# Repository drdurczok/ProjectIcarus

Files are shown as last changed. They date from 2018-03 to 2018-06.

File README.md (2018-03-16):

# ProjectIcarus
A mechanical hand with the full dexterity of its real counterpart controlled in an intuitive way by a human. The control will be based on the idea of mimicking the operators limbs. Pairing this with a strategically placed camera and a virtual reality headset, we have an operator who is fully immersed and in full control of the situation at hand.

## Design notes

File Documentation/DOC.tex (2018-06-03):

\documentclass{article}
\usepackage{graphicx}
\usepackage{color}
\usepackage{url}
\usepackage[font=small,labelfont=bf]{caption}
\usepackage[a4paper, total={16cm, 24cm}]{geometry}
\usepackage{indentfirst}

\begin{document}

\begin{titlepage}
    \begin{center}
        
	\begin{figure}
		\centering
        FACULTY OF MECHANICAL ENGINEERING AND ROBOTICS\\
        AGH UNIVERSITY OF SCIENCE AND TECHNOLOGY\\
        \vspace{0.2cm}
    	\begin{minipage}[b]{0.4\textwidth}
    	    \centering
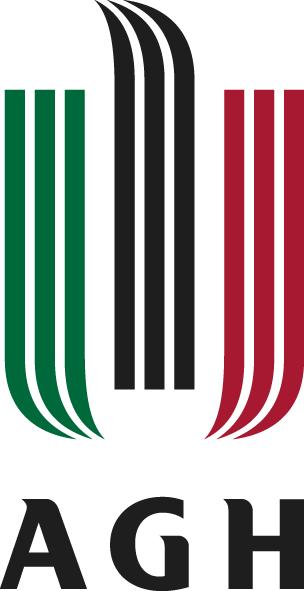
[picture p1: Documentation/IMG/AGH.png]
    		
    	\end{minipage}
    	\hfill
    	\begin{minipage}[b]{0.4\textwidth}
	    	\centering
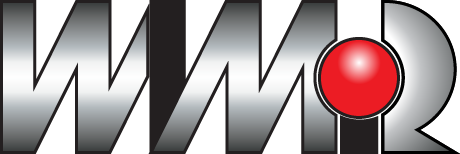
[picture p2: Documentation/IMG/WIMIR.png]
    		
		\end{minipage}
		\vspace{1cm}
    \end{figure}

    \Huge \textbf{Vision Controlled Mechanical Hand}
        
    \vspace{0.8cm}
    \LARGE 
    \color{black} 
            
    \vspace{0.8cm}       
    \textbf{Damian Durczok\\Mikolaj Gacek\\Adam Kolusz}        
    \vfill       
    \vspace{0.8cm}    
    3.06.2018
        
    \end{center}
\end{titlepage}

\tableofcontents
\break

\section{State of Art}
A typical mechatronic device encompasses many fields of technological engineering. This includes mechanical engineering, electronics, computer engineering, systems and control engineering. To thoroughly design such a system with awareness of all its elements during each step of the process requires the foresight and knowledge of all the components and relations between individual elements. This is the purpose of the state of art - a prerequisite to the initialization of a project. By the end of this section we will have explored existing technologies and solutions to our problem and drawn up a basic model of the mechatronic device.

\subsection{The Problem}
Certain situations that endanger human life benefit from the intervention of a robotic device. However, these robots may be limited in functionality compared to the human counterpart. In cases such as bomb disposal, nuclear power station decommissioning or handling of dangerous substances the dexterity of a human hand is significantly important.

\subsection{The Solution}
The mechanical hand is a device that has been iterated on many times in recent history. Control of such a hand is either by machine or human. For automated tasks, a machine controlled hand is more than sufficient. However, in unpredictable environments human intervention is still necessary.

This is where the idea stems together. A mechanical hand with the full dexterity of its real counterpart controlled in an intuitive way by a human. The control will be based on the idea of mimicking the operators limbs. Pairing this with a strategically placed camera and a virtual reality headset, we have an operator who is fully immersed and in full control of the situation at hand.

\subsection{Mechanical Hand}
Most modern innovations of the mechanical hand are related to the development of prosthetics. BeBionic \cite{bebionic} and Vincent Systems \cite{vincent} among many others have developed such devices that accurately mimic the likeness.

\begin{center}
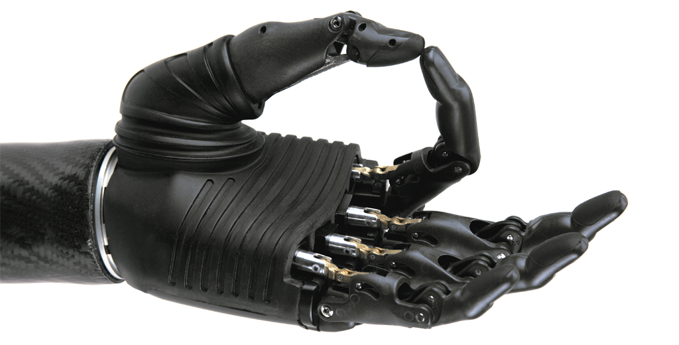
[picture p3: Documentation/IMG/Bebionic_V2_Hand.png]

\captionof{figure}{BeBionic Mechanical Hand}
\end{center}

The most popular actuation method is a combination of a DC motor and either a worm gear or lead screw. The size of the hand leaves us with a very small working area, as a result the driving motors must be very small with high gear reductions.

\begin{center}
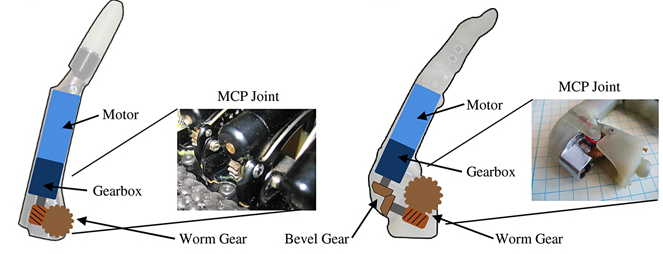
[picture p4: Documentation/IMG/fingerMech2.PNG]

\captionof{figure}{Mechanics of a finger \cite{JRRD}}
\end{center}

Another issue to contend with is the weight and speed of the mechanism. For prosthetic use, the hands are made to be lightweight for mobility. Whereas in our application this isn't a problem, we may still benefit from reducing the moments of inertia by increasing the acceleration capabilities of joints. Ideally having the same dynamic properties as the human hand.

The limited working space also forces certain optimization. For instance, not all joints need to be independently driven. We may simplify the model by involving mechanisms that create a fixed relationship between joints.

\begin{center}
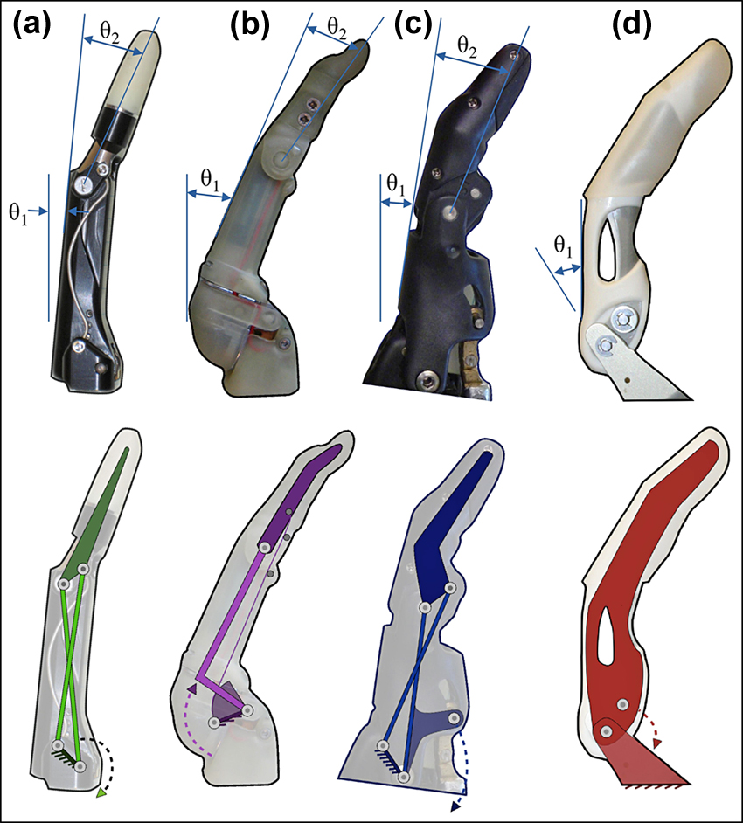
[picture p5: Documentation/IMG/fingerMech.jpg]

\captionof{figure}{Reducing degrees of freedom mechanically \cite{JRRD}}
\end{center}

A final feature commonly observed is a certain flexion compliance level. Under a certain level of pressure, the joint flexes by either a spring or flexible material. This is a protective measure to prevent the damage of certain elements.

Many hobbyists opt out for a different solution that includes a motor and line. The joints are controlled in one direction by the contraction of a line and in the other by a spring or flexible material. This greatly simplifies the design process by allowing the motors to be located elsewhere. Potentially allowing for much larger drives and a greater gripping force along with greater movement speeds and accelerations. This system also naturally includes flexion compliance.

\begin{center}

\captionof{figure}{Solidworks solution \cite{stringHand}}
\end{center}

This solution isn't as well researched as the earlier method and will require a longer prototyping phase. \\[12pt]
\indent Pneumatics may offer another solution. All the fingers are actuated by a pneumatic air muscle. These prove to have very high grip strength with favourable dynamic characteristics. All however comes with the price of size, to drive such a system a constant supply of compressed air is necessary to accurately position the stroke-length of each air muscle. Additionally a large valve system is necessary to control such a device.

\begin{center}
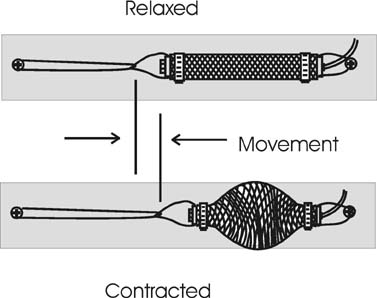
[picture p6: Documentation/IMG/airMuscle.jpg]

\captionof{figure}{Air Muscle}
\end{center}

In summary, we may consider driving our mechanism with either an electric motor or a pneumatic device. The pneumatic device may allow for much better dynamic performance such as limb velocity, acceleration and grip strength. However requires an entire pneumatic system in place which may prove expensive and resource heavy. The DC motor compromises on dynamic performance in place for a more ergonomic design.\\[12pt]
\indent The driving mechanism may be optimized by involving dependent joints. These joints may be driven directly or at a distance using lines. A line driven mechanism alleviates the problem of having to work in a small working area by removing the largest elements externally. 

\subsection{Sensors}
For the human hand to control the mechanical counterpart a set of sensors are necessary. For simplicity, we will only track the position of individual fingers. Although data sets such as grip strength, velocity or acceleration of fingers may inadvertently be natural features of some of the concepts.

A vision system introduces a non-invasive and non-contact method. Free to the public libraries such as OpenCV paired with a stereo camera system allow for creation of depth perception maps. After calibration of each camera and synchronization of frames, such a system will allow for accurate tracking.

\begin{center}
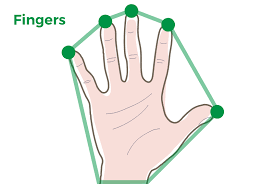
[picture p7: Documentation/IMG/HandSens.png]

\captionof{figure}{Visualization of hand recognition software}
\end{center}

\indent Microsoft released another interpretation of a motion sensing input design with the Xbox Kinect \cite{kinect}. The device includes an additional IR light source and an infrared camera for depth mapping and an RGB color VGA video camera for image recognition. The camera is capable of isolating the human from the background and with image recognition track individual limbs. The Microsoft SDK package for the system also includes access to the massive database for image recognition. This has been shown to work with small children using sign language learning software.

Plenty of other approaches also exist. One of the most popular is the usage of flex sensors. The concept is very simple, a change of resistance occurs with deflection, ie the flexing of a joint. The main disadvantage of such a solution is very low cost/efficiency ratio. However this method takes up very little space and low power consumption.

Another accurate positioning method is with the use of multiple MPUs placed in carefully selected positions. If connected via a I2C protocol we may connect many along a single bus. These sensors are quite inexpensive compared to the flex sensor and provide acceptable accuracy when paired with suitable filters such as a Kalman filter. If not taken into account, the position obtained drifts over time resulting in a high error. However this can easily be mitigated.

With a strategically placed camera and a line emitting IR blaster we may create a vision system that proves to be much more reliable than the previous concept. DIGITS \cite{Digits} is the realization of such a device. It is capable of emulating the human hand in a virtual environment with great success.

\begin{center}
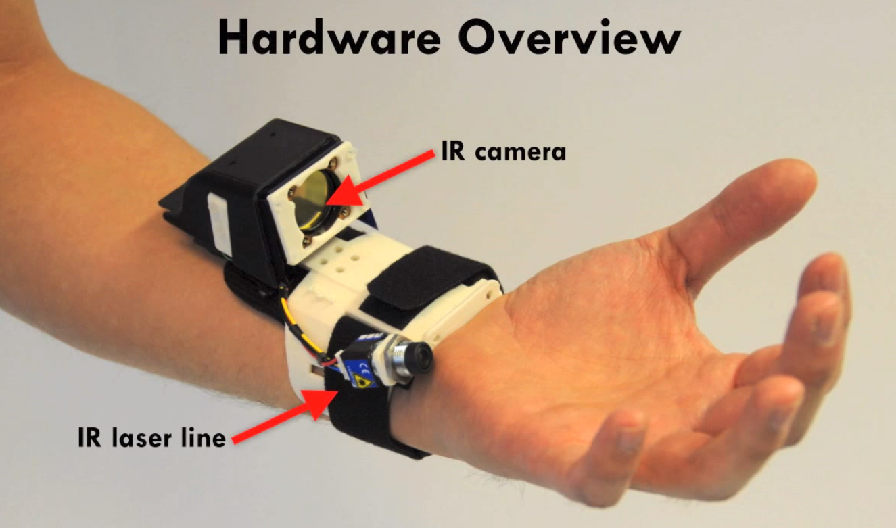
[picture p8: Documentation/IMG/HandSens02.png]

\captionof{figure}{A finger position method by Digits \cite{Digits}}
\end{center}

\indent The IR blaster greatly increases the image recognition performance by giving it obvious vision cues. The wrist mounted device may also benefit from an additional MPU sensor that will provide us with information on the placement of the arm. Such a system is not limited by the environment; lighting levels and surrounding colors wouldn't have a significant impact on the performance of the mechanism.

\subsection{Control}

For an electronic control system we may consider two distinct architectures that will be ideal for our device; an FPGA board or a microcomputer like the Raspberry Pi. Both devices are capable of image signal processing with the use of the OpenCV library, therefore all techniques discussed above are viable. In extension, OpenCL (an official and supported extension to OpenCV) can be used inplace of HDL in FPGA to improve design productivity. The main advantage of FPGA over a CPU is parallelism\cite{FPGA}. In a system where many sensors and actuators are present, and a quick response of a mechanical hand is essential this can become a major advantage over traditional microcomputers. However, this comes with a cost of complexity.

Both systems are also capable of signal filtering and noise reduction. This can reduce micro motions and sensor imperfections to create a much more fluid movement of the hand. Additionally, machine learning could incorporate a decision making process that could create precise maneuvers even if the operator isn't fully trained or capable of them.  Potentially becoming an enhanced extension of the human by providing stability and limiting the motion to avoid accidental jerks or unwanted reflexes.

\section{Concept}
\subsection{Mechanics}

The primary attributes of our mechanical hand will be its gripping capabilities and precision. To achieve this while keeping the entire project within acceptable dimensions we need to introduce dependent joints with certain flexion compliance.

Some of the dependent joints will have an additional mechanism extended from it. This mechanism will usually consist of a spring that is pushing on a lever. With no external forces, the lever will be sitting in a locked maximum position. The moment it comes into contact with something and depending on the amount of force applied, the lever hinges back. This gives the dependent joint a certain amount of restricted movement that mimics the joints of the hand in a similar fashion. This sort of compliance will greatly increase the hands holding capabilities by being able to mechanically adapt to the objects geometrical features.

A single hand will be comprised of three digits, each with two degrees of controlled motion. However, due to flexion compliance it will have many more degrees of freedom. The human hand has four bones for each finger and three for the thumb. The bones go as follows from the tip of the finger to the wrist; distal phalanges, medial phalanges, proximal phalanges and the metacarpals. With the thumb lacking the medial phalanges. Each finger has four degrees of freedom except for the thumb by only having three. Next we will explore all our joints and describe how we plan to resolve them. 

The first is the opposable thumb, which will have two joints and one degree of controlled motion. The distal phalanges will have flexion compliance, while the metacarpal will be driven by a larger motor to match the cumulative force of the other joints. The thumb needs to be as universal as its counterpart. Both grip strength and precision tasks paired with the other fingers are important. 

The index finger will have four joints and also two degrees of motion. The distal phalanges will have 90 degree flexion compliance and is dependent on the angle of the medial phalanges. The medial phalanges and proximal phalanges will be each driven by a motor, while the metacarpals will be attached by ball joint and given minimal flexion compliance.

The final three fingers will be combined into one larger finger. Since these fingers are usually used for gripping and handling of objects, they will be mounted with larger motors and the larger surface area will provide a better gripping surface. The joint mobility will be similar to the index finger.

The last area to cover is the palm. The metacarpals is responsibly for its shape. We have two metacarpals that have flexion compliance and one on the thumb that is driven. This means the palm has the capability of adjusting its shape to a gripped object.

\subsection{Control and Sensors}

With the mechanical end of the project providing advantages gripping mechanisms and variable grip strength, the control of the device may be much more forgiving and the use of haptic feedback isn't as necessary. With this in mind, we may create a completely non invasive human operated controller with the use of vision systems.

The system will be made up of two cameras that will provide stereo vision. With proper calibration, we may produce a depth map and isolate a human operator from the background. Once isolated, it is a matter of manipulating the image and developing algorithms that may track geometrical features. Libraries such as OpenCV already provide most of these features in languages such as Python and C++.

The readings from the camera may be further improved by adding a layer of machine decision making. Certain filters for noise reduction are certainly necessary, however we may also include pre-programmed operations that may assist the human and become an extension of him. For instance, we may limit the velocity of fingers to reduce abrupt movements in certain situations or remember the gripping position for a certain object. This way the operator carries out the general movement required of the robot and the robot decides on the precise movements that may be difficult for the user to control. 

\subsection{Electronics and Actuating}

Since the image signals from two cameras have to be processed in real-time it is important to consider a capable computer. We decided that the entire Vision System will be run on Raspberry Pi 3 Model B microcomputer. This device possesses a quad-core 64bit processor and 1GB RAM, hence is capable of performing desired operations. Further reassurance of its capabilities is the many camera modules and OpenCV projects already developed for the Raspberry.

The robotic fingers will be actuated by six servomotors controlled by an Arduino Uno R3 attached to the hand. The Arduino Uno R3 has 14 digital input/output pins (of which 6 can be used as PWM outputs). The wireless connection between the Raspberry Pi 3 B and the Arduino will be implemented with the use of a Bluetooth protocol. The Raspberry has a built-in Bluetooth module and Arduino can be easily extended with a HC-0x series Bluetooth module.

The Arduino controller and motors will be energized by an individual power supply with a voltage stabilizer. The Raspberry Pi will be energized by a set of 18650 cells through a voltage stabilizer.

\break
\section{Software}
\subsection{Requirements}
Requirements analysis is the first stage in the systems engineering process and software development process. The software requirements specification (SRS) lays out functional and non-functional requirements, and may include a set of use-cases that describe user interactions that the software must provide. We will carry out such an analysis on our system.

The purpose of this software is simple, to track the movements of a human hand. Specifically, we need to obtain certain points correlated to the human hand that satisfy our kinematic equations. The system will have to operate in real time with minimal delays. This system must also be non-invasive and work reliable in many different environments. Our solution implements a vision system. The general structure will look as such; capture footage, process the video feed, analyze the data and implement filters or statistical methods to improve the tracking. The product must work with minimum product knowledge, so called plug-and-play.

The user will interact with the system through both the vision system and voice controls. The camera system will be operating at a distance from the user, therefore to implement a user interface that is convenient to use and continues to be non-invasive and non-contact, as the hands are preoccupied, we will be relying on voice actuation. This will provide basic functionality on top of the core tracking service. 

We will also be communicating with another device, which in turn is responsible for controlling the mechanical hand. The information processed by our software will provide the secondary device with the information it needs to carry out the inverse kinematic calculations. This information will be in the form of coordinate points. This process must be robust with very fast response time. The quality of the point detection must be reliable and stable. It must also be tolerant to any user mistakes.

Additional limitations to our software will involve the hardware it will be run on. Our system will be limited to the capabilities of the Raspberry Pi, as well as the available libraries. Our vision system will be built on the OpenCv library, while our voice actuation on the Sphinx libraries. Both libraries support C++ and Java.\vspace{12pt}

The software aims to provide natural control for complex end-effectors. The human brain is very good at calculating inverse kinematics of its own body, to the point where it is completely natural to us without much thought. By taking advantage of this, we may quicken the learning process for controlling advanced machinery and allow for much more complex maneuverability. Controlling a mechanical hand is one possible use-case, however by selecting what points and how many points are to be tracked, this software may be used for many different types of control, not necessarily mechanical. The software may be just as easily used for gesture control or interpreting sign language. Extensibility needs to be considered during the design process. Additionally, we may provide options for several different supported cameras and tracking modules and expand these features over time with software updates.

\subsection{Implementation}
We may break our entire software apart into several subcategories; vision system, vision system calibration, audio system and audio system calibration. The calibration software will be used by the developers to prepare certain models to work with our software, this will be discussed in much more detail below. The user will be interacting exclusively with our vision and audio software.
\subsubsection{Vision System Calibration}
The calibration process is made up of several key steps depending on the technology used. First let us look at the calibration of a stereo camera setup for the creation of disparity maps. We begin by calculating the intrinsic parameters of each camera, this includes the focal length, principle points and consequently the distortion coefficients. We use this information to undistort each individual camera. Following this, we need to calculate the extrinsic parameters. During this process we acquire information of where one camera is with respect to the other, this includes the rotation and translation matrix. From this we additionally acquire the fundamental and essential matrix, which in turn gives us the rectification parameters. After rectifying the images, we will have matching epipolar lines in each camera and we may begin the disparity mapping process. The disparity map gives us clear information on the hands location and its shape. The actual tracking software will be discussed later.

\begin{figure}[!hb]
    \begin{minipage}[b]{0.49\textwidth}
    	   \centering
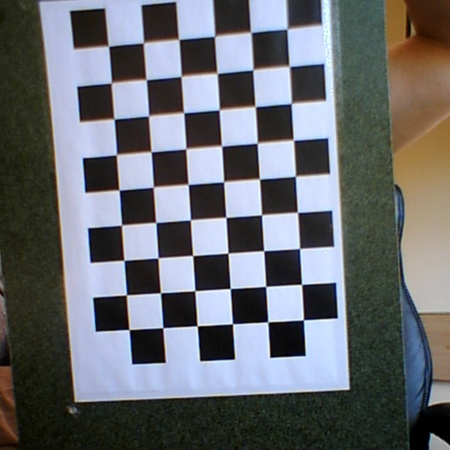
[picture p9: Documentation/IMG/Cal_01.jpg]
		
		\captionof{figure}{Calibration Image}
	\end{minipage}
    \hfill
    \begin{minipage}[b]{0.49\textwidth}
	    \centering
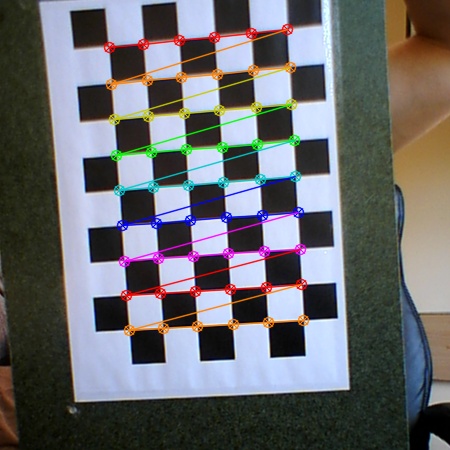
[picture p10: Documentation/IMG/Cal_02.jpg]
		
		\captionof{figure}{Calibration Image With Overlay}    	
	\end{minipage}
\end{figure}

In the case of an IR blaster setup, the calibration will look slightly different. Since we will only be using one camera to create a disparity map, the calibration will be much simpler. After calculating the intrinsic parameters, the camera should be ready.
\subsubsection{Vision System}
The vision system will be comprised of several steps. The first being to discern the hand from other objects and background noise. This will be done with the use of disparity maps and thresholds. After obtaining a clearly defined silhouette of the object to be tracked, we focus on the original video feed again and pattern the singled out area with a grid of points. These points will be used in our Lucas-Kanade tracking algorithm that will create optical flow vectors for each of the given points. This will provide us with displacement and velocity information. The next step requires another set of algorithms that first filter any errors in the optical flow map and then using statistical methods returns a few individual points that correspond to the hands position in 3D space.

\begin{center}
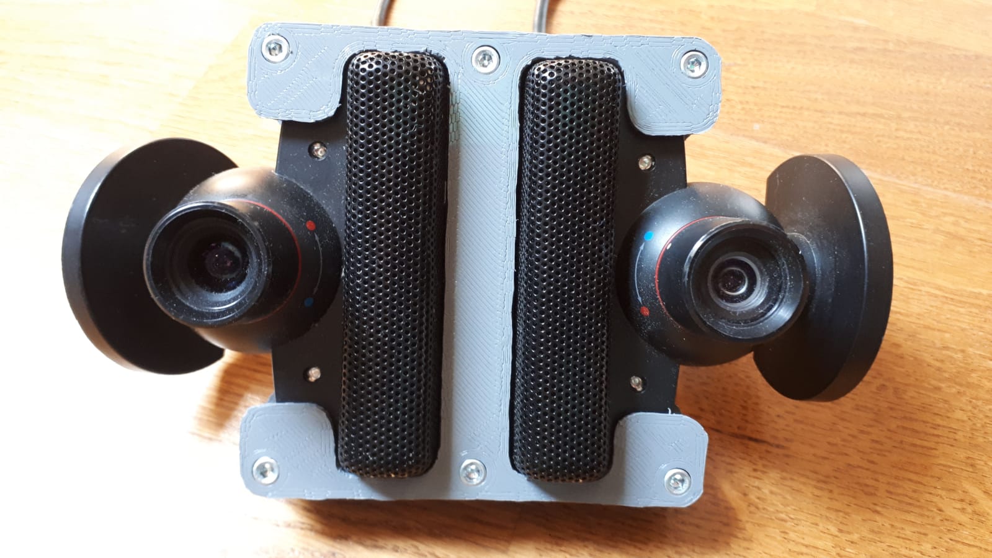
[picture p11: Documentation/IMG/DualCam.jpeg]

\captionof{figure}{Dual Camera Setup}	
\end{center}

\break
Here we may compare the two very different technologies. The dual camera system relies on very precise calibration to create accurate epipolar lines. These lines reduce the number of calculations needed to find matching points as they are used as lines along which the pixels are compared between images. That is why we have noise present along what seems like horizontal lines, better calibration would reduce those. A disadvantage of such a system is that there needs to be consistent light levels for this to work. Most environments do not provide a bright and reliable light source, therefore some additional preparation is necessary for such a system to work consistently.

The Kinect on the other hand uses infrared light to create a grid of points. It uses its IR camera to measure the size of various points and gauge their distance. Based on all this data it is capable of creating a disparity map. Additionally, since it creates its own source of invisible light, it will work in various situations where the dual camera set-up wouldn't. The Kinect relies on complex algorithms only provided by Microsoft Windows and their SDK packages. The reason the Kinect is so reliable is because of the machine learning done at Micosoft to make the software capable of such tasks.

\begin{center}
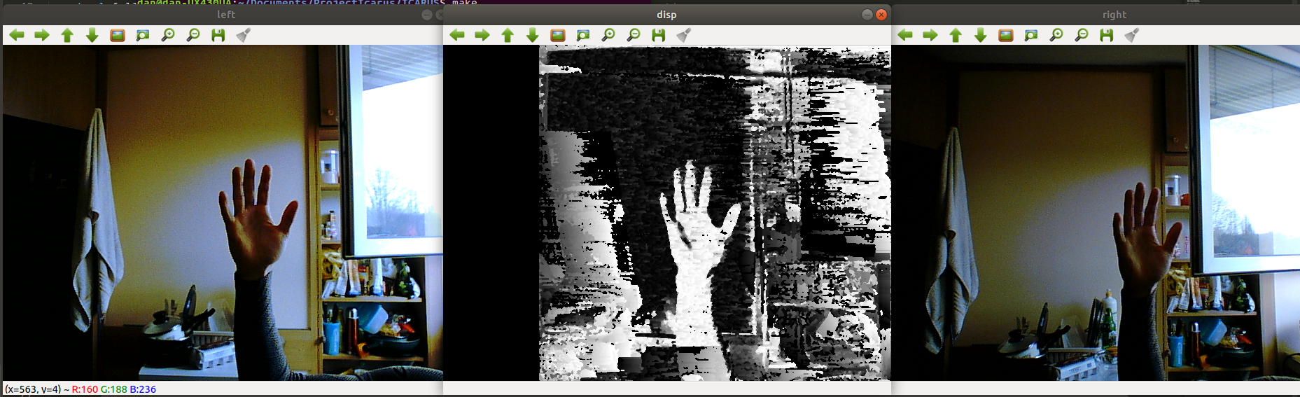
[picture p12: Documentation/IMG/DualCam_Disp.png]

\captionof{figure}{Dual Camera Disparity Map}   	
\end{center}

\begin{figure}[!hb]
    \begin{minipage}[b]{0.49\textwidth}
    	   \centering
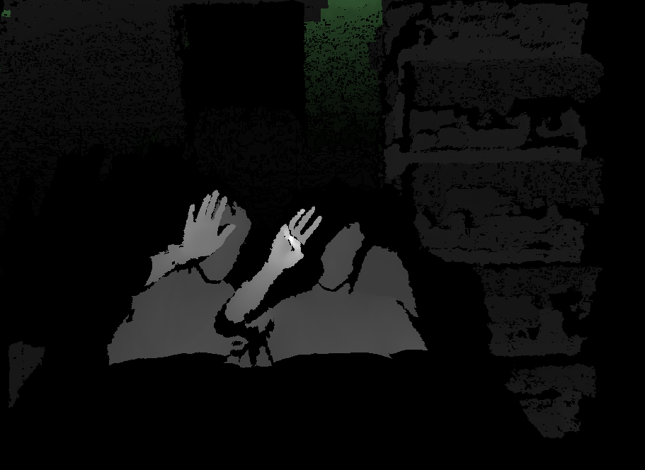
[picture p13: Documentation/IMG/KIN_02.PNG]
		
	\end{minipage}
    \hfill
    \begin{minipage}[b]{0.49\textwidth}
	    \centering
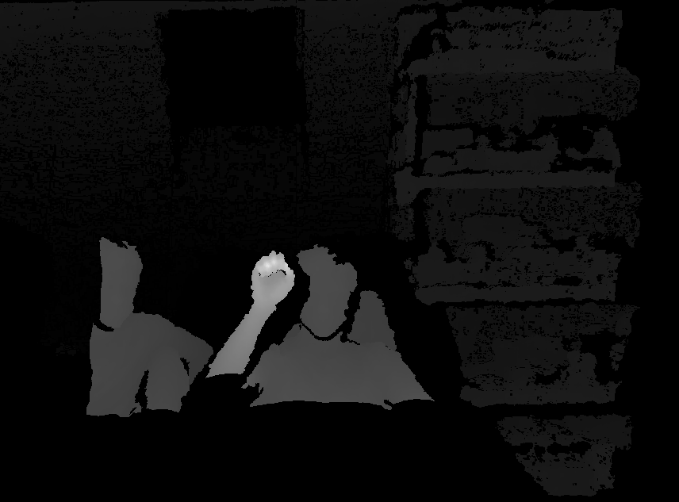
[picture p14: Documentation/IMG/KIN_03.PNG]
		
	\end{minipage}
	\captionof{figure}{Kinect Disparity Map}
\end{figure}

\subsubsection{Audio System}
The general process of the application consists of several key steps. We begin with interval audio recordings. After each interval recording, it decodes the .raw file and searches for a keyword. If the keyword was spoken, the recording re-initiates. The second .raw file is decoded to receive a string. This string needs to be compared to the applications look up table. The final part is the calling of the function which is most appropriate based on the returned string. 
Many other classes make up the individual actions of the application. These “action” classes are very easy to add and are what makes the program modular. 
To accomplish all of this we needed to take advantage of language and audio processing API’s. These are briefly introduced and summarized below:

\paragraph{PocketSphinx} 
Pocket-Sphinx is a lightweight speech recognition engine, specifically tuned for handheld and mobile devices. The libraries are written in C and are dependent on the Sphinx-Base library. \vspace{12pt}

\noindent For the library to function properly, we need to provide additional models and dictionaries:
\begin{itemize}
	\item Acoustic model: The acoustic model models the sound of a phone, it translates recorded sounds into labeled phones. Usually a hmm is used. Each phone has a hmm. 
	\item Phonetic dictionary: Maps phones to words.
	\item Language model: Used to determine sequences of words that are allowed. 
\end{itemize}

\noindent Most models require training to be more accurate:
\begin{enumerate}
	\item Acoustic models require lots of recordings of people saying words and sentences (not that difficult to do) and accurate transcription of the recordings (time consuming). It is possible to take an existing model and quickly adapt it to a particular speaker.
	\item Language models require for different systems different language models. Different applications need to recognize different sets of words.
	\item The performance of the recognizer is significantly improved if your language model only considers relevant words to your application.
	\item You can take an existing language model and trim it to what you need, or make on from scratch using the JSGF format.
\end{enumerate}

Words are a sequences of sounds, where each sound is a phone. However, the exact pronunciation of a phone depends on the phones before and after.
Diphones are two phones. Diphones are less impacted by the phones that come before or after. 
Senones are triphones and quinphones.
While there are many phones, not all combinations of a phone is a word. Thus, we should not simply recognize phones, but we need to recognize words which are sequences of phones.
Besides phones are fillers (ex., breath, “um”). An utterance is a sequence of words and fillers. Utterances are separated by a pause.

\paragraph{ALSA(Advanced Linux Sound Architecture)}
Sound is converted to its electrical form by a transducer, such as a microphone. An analog-to-digital converter (ADC) converts the analog voltages into discrete values, called samples, at regular intervals in time, known as the sampling rate. By sending the samples to a digital-to-analog converter and an output transducer, such as a loudspeaker, the original sound can be reproduced.

The size of the samples, expressed in bits, is one factor that determines how accurately the sound is represented in digital form. The other major factor affecting sound quality is the sampling rate. The Nyquist Theorem states that the highest frequency that can be represented accurately is at most one-half the sampling rate. 

We will mostly be interested in the PCM interface: the interface for managing digital audio capture and playback. 

 A sound card has a hardware buffer that stores recorded samples. When the buffer is sufficiently full, it generates an interrupt. The kernel sound driver then uses direct memory access (DMA) to transfer samples to an application buffer in memory. Similarly, for playback, another application buffer is transferred from memory to the sound card's hardware buffer using DMA.
 
These hardware buffers are ring buffers, meaning the data wraps back to the start when the end of the buffer is reached. A pointer is maintained to keep track of the current positions in both the hardware buffer and the application buffer. Outside of the kernel, only the application buffer is of interest, so from here on we discuss only the application buffer.
The size of the buffer can be programmed by ALSA library calls. The buffer can be quite large, and transferring it in one operation could result in unacceptable delays, called latency. To solve this, ALSA splits the buffer up into a series of periods and transfers the data in units of a period.
A period stores frames, each of which contains the samples captured at one point in time. For a stereo device, the frame would contain samples for two channels.

\begin{figure}[!hb]
    \begin{minipage}[b]{0.49\textwidth}
    	\centering
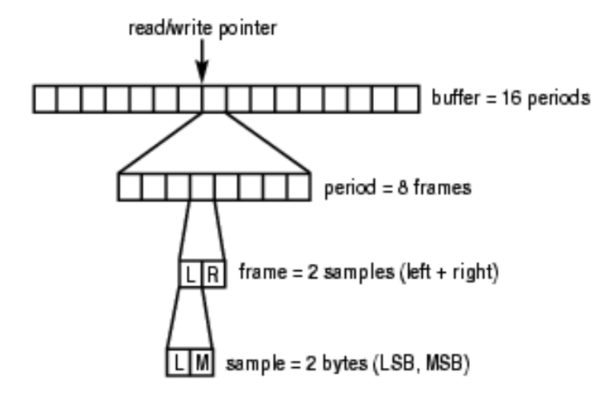
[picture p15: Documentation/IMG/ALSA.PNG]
		   	
	\end{minipage}
    \hfill
    \begin{minipage}[b]{0.49\textwidth}
		The Application Buffer (Over and Under Run), illustrates the breakdown of a buffer into periods, frames and samples with some hypothetical values. Here, left and right channel information is stored alternately within a frame; this is called interleaved mode. A non-interleaved mode, where all the sample data for one channel is stored followed by the data for the next channel, also is supported.\vspace{12pt} 	
	\end{minipage}
\end{figure}

When a sound device is active, data is transferred continuously between the hardware and application buffers. In the case of data capture (recording), if the application does not read the data in the buffer rapidly enough, the circular buffer is overwritten with new data. The resulting data loss is known as overrun. During playback, if the application does not pass data into the buffer quickly enough, it becomes starved for data, resulting in an error called underrun. The ALSA documentation sometimes refers to both of these conditions using the term XRUN. Properly designed applications can minimize XRUN and recover if it occurs.

\noindent Programs that use the PCM interface generally follow this pseudo-code:
\begin{itemize}
	\item open interface for capture or playback
	\item set hardware parameters (access mode, data format, channels, rate, etc.)
	\item while there is data to be processed:
	\begin{itemize}
		\item read PCM data (capture)
		\item write PCM data (playback)
	\end{itemize}
	\item close interface
\end{itemize}
	
When we open the PCM stream, we specify the mode as SND\textunderscore PC\textunderscore STREAM\textunderscore CAPTURE. In the main processing loop, we read the samples from the sound hardware using snd\textunderscore pcm\textunderscore readi and write it to standard output using write. 

In order to set the hardware parameters for the stream, we need to allocate a variable of type snd\textunderscore pcm\textunderscore hw\textunderscore params\textunderscore t. We do this with the macro snd\textunderscore pcm\textunderscore hw\textunderscore params\textunderscore alloca. Next, we initialize the variable using the function snd\textunderscore pcm\textunderscore hw\textunderscore params\textunderscore any, passing the previously opened PCM stream. 

We now set the desired hardware parameters using API calls that take the PCM stream handle, the hardware parameters structure and the parameter value. We set the stream to interleaved mode, 16-bit sample size, 1 channel and a 44,100 bps sampling rate. In the case of the sampling rate, sound hardware is not always able to support every sampling rate exactly. We use the function snd\textunderscore pcm\textunderscore hw\textunderscore params\textunderscore set\textunderscore rate\textunderscore near to request the nearest supported sampling rate to the requested value. The hardware parameters are not actually made active until we call the function snd\textunderscore pcm\textunderscore hw\textunderscore params.

\break
\section{Kinematics}
\subsection{Index Finger}
We will begin the analysis with the index finger. The mechanical finger may be represented by a simplified kinematic model presented below. Our system has two degrees of freedom, however the structure is much more complicated due to various lever systems and dependent angles. To simplify our mechanism, we may divide the system into four subsystems. Each system will have its own set of equations that will eventually be put together in a programming environment to define the movement of the finger.

\begin{center}
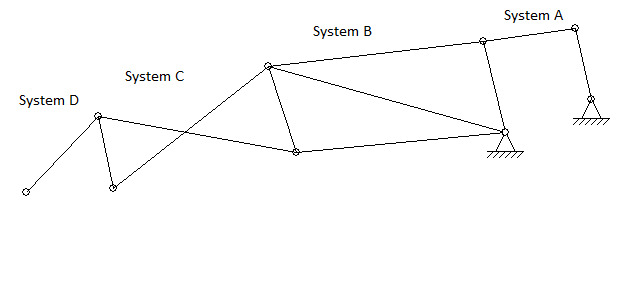
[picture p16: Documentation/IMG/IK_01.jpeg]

\captionof{figure}{Kinematic Model}	   	
\end{center}

Inverse kinematics for system A. This system is a simple 4 bar linkage mechanism that consists of a crank, coupler, rocker and frame. The motor attaches to the crank and drives the proximal phalange. The motor angle $\varphi$ drives $\alpha$, therefore the inverse kinematic formula has only one unknown variable $\alpha$ that is provided by system B. The rest of the formula consists of constants that are properties of the system. \textbf{\textit{All calculations are provided in the appendix.}}

\begin{center}
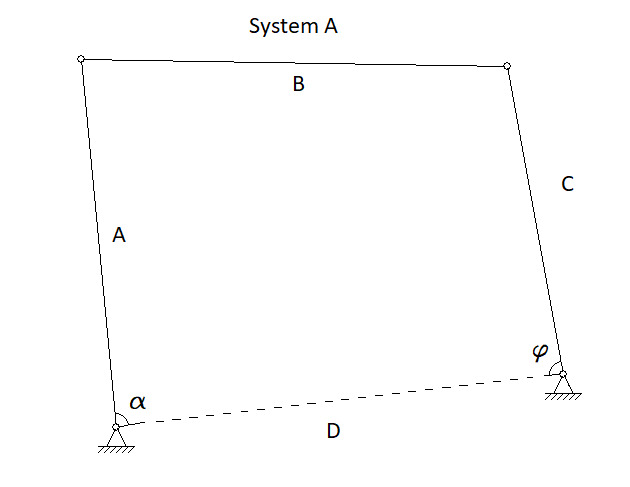
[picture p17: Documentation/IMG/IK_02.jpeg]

\captionof{figure}{4 bar linkage mechanism}	   	
\end{center}

\[ \varphi = sin^{-1} \bigg(\frac{Asin\alpha}{\sqrt{A^2+D^2-2ADcos\alpha}}\bigg) + cos^{-1} \bigg(\frac{A^2+D^2-2ADcos\alpha-B^2+C^2}{2C\sqrt{A^2+D^2-2ADcos\alpha}}\bigg)\]

Inverse kinematics for system B. This is the simplest possible system being a simple lever. However due to the software constraints, we have to additionally consider the orientation of the base coordinate system (the palm) and the offset from the motors 0 degree position. The formula is provided with the X coordinate from the camera system and based on this information figures out the angle on the four bar linkage mechanism.

\begin{center}
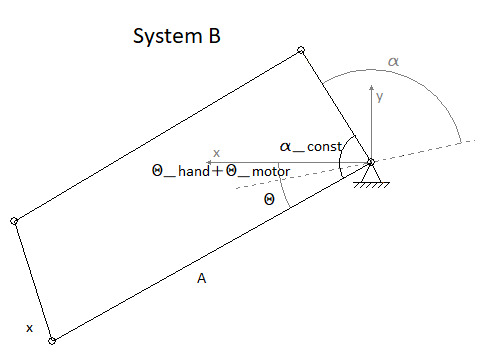
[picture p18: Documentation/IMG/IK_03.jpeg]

\captionof{figure}{Proximal Phalange}	   	
\end{center}

\[ \alpha = cos^{-1}\bigg(\frac{X}{A}\bigg) - (\theta_{hand} + \theta_{motor}) + (\pi - \alpha_{const}) \]

Provided the two equation above, we have everything we need to control the proximal phalange with the first servo motor. The servo motor is controlled entirely by one X axis coordinate provided by the software. The equations take into account various offsets, such as the orientation of the palm, as well as properties of the system such as orientation of the motor. To optimize the geometry, we may use the first equation to equate a certain rotation of the motor to the angular displacement of the finger.\vspace{12pt}

The second part of the finger is much more complicated. The mechanism is a crossed four bar linkage, which significantly complicates the equations. First we will provide several formulas that create dependencies between various angles of the mechanism.

\begin{center}
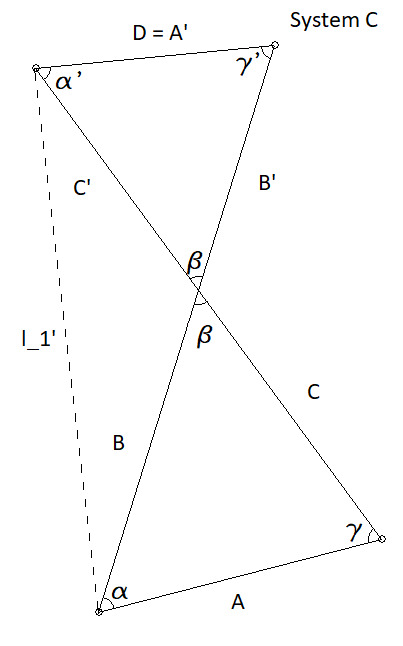
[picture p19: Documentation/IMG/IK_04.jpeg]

\captionof{figure}{Crossed 4 bar linkage mechanism}	   	
\end{center}

This formula provides us with the length the driving string needs to shorten. The only unknown is $\gamma$.
\[ l_1' = \sqrt{A^2+C^2-2ACcos\gamma}\]

This formula is taken as a proportion of the two triangles formed by the crossed mechanism. It helps us relate opposite angles.
\[ C' = \frac{CA'}{A} \frac{sin\gamma'}{sin\gamma} \]

Based on the equations above and a few more tricks, we are able to relate both angles from one side of the crossed four bar linkage mechanism. At this point we have all the information required to continue our calculations.
\[ \gamma' = cos^{-1}\bigg( \frac{-A^2+B^2-C^2+D^2+2ACcos\gamma}{-2CD} \bigg)\]

\[ \alpha = sin^{-1} \bigg( \sqrt{\frac{Bsin\gamma-(C-C')sin\gamma'}{C'}} \bigg) \]

The formula above may be used for an inverse kinematic system for the medial phalange, which is what is included in the Arduino. The last formula is much too complicated to derive for an inverse kinematic system, therefore a numeric solution is necessary. With the forward kinematic equation below, we may create a look up table and relate both $\gamma'$ and $\alpha$ to $\gamma$ which in turn provides us with the necessary information to calculate the shortening of the string and movement of the motor.

\begin{center}
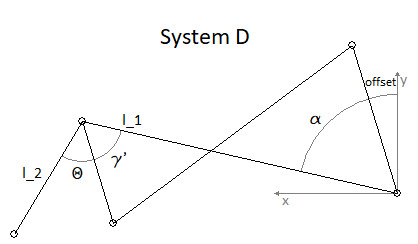
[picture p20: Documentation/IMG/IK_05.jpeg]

\captionof{figure}{Distal Phalange}	   	
\end{center}

\[ X = l_1 cos(\alpha+offsets) - l_2 cos(\gamma') \]

\subsection{Thumb}
Although the thumb has two degrees of freedom as in the previous example, it is much simpler. Both joints are rotational, however in two different planes. The forward kinematics as well as the inverse kinematics are both relatively simple.

\begin{figure}[!hb]
    \begin{minipage}[b]{0.49\textwidth}
    	\centering
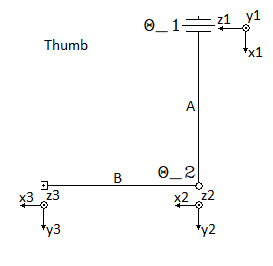
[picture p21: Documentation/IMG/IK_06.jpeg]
		
	\end{minipage}
    \hfill
    \begin{minipage}[b]{0.49\textwidth}
		\[ \theta_1 = cos^{-1}\bigg(\frac{X_3}{A}+B*sin(\theta_2)\bigg)\]
		\[ \theta_2 = cos^{-1}\bigg(\frac{X_2}{B}\bigg) \]\vspace{80pt} 	
	\end{minipage}
\end{figure}

\subsection{Arduino}
The formulas derived earlier are for the purpose of controlling the hand, therefore they need a controller. The Arduino Nano is the board of choice being that it is very similar to the Arduino UNO (where all the testing was done) and is very compact. The Atmega328's 8-bit CPU running at 16MHz is more than sufficient for calculating our equations in real time. The Nano has only 6 PWM pins, however the provided servo libraries support many more. A servo only requires a pulse 1ms long, so a driving frequency of 1kHz is needed. Such a frequency is easily accomplished by the integrated CPU and we may actually use any of the outputs on the device. The 14 digital pins and 8 analog summed up for a total of 22 pins is more than sufficient for wiring up our device. The servo motors are powered by an external power supply, therefore the Arduino Nano has the sole task of controlling the motors.

\begin{center}
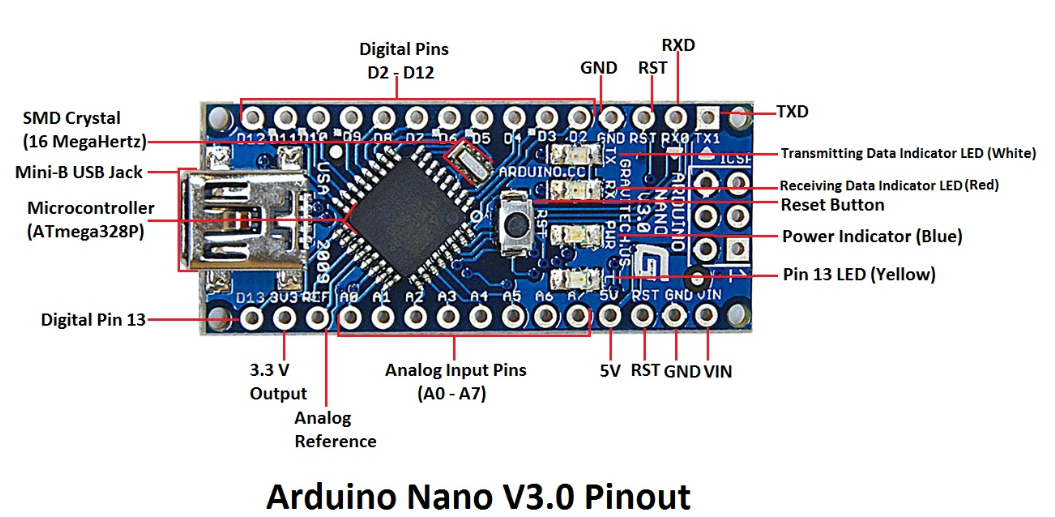
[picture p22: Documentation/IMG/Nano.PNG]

\end{center}

An external device will provide the parameters necessary for our equations. We will  now review the code structure. For each motor, there exists a separate INO file that contains all the necessary equations and conversions in reusable methods. This allows us to reuse many of the formulas for fingers with the same kinematics. Additionally, there exist parameter files that carry the mechanisms properties. Our external input device provides us with the X coordinates for each motor. There is one input, a coordinate, and one output, the angle of the motor, per servo.

There exist only two different mechanism, the thumb and index finger. Therefore four different kinematic structures for two degree of freedom mechanisms. The index finger is reusable, varying only in mechanical properties in configuration files. Each INO file has a debugging tool that displays various values of interest. Below we may find the first one for the proximal phalange of the index finger.

\begin{center}
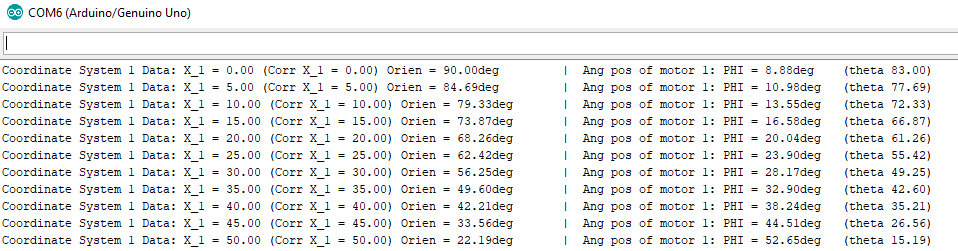
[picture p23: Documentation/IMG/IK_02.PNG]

\end{center}

We may interpret the data in the following fashion. The X1 information is provided by the external device as input to our code. If X1 is zero, this means it is at a 90 degree angle to the world coordinate system (or if palm orientation compensation is disabled, 90 degrees to the palm). The corrected X1 value takes into account angular offsets, for instance if the palm is angled, so is the world coordinate system and the X1 value needs to be properly adjusted to accurately represent the data. The angle of the motor is PHI, the data was compared to the real world range of motion and proves to be correct. If we look at X1 = 0, we may notice the motor starts at 8 degrees. This is because the motor is offset from the base coordinate system and this needs to be taken into account as we did in the kinematic formulas. The mechanical properties INO file contains additional sketches that demonstrate the exact locations of parameters.

We may now take a look at the medial and proximal phalange drive of the index finger.

\begin{center}
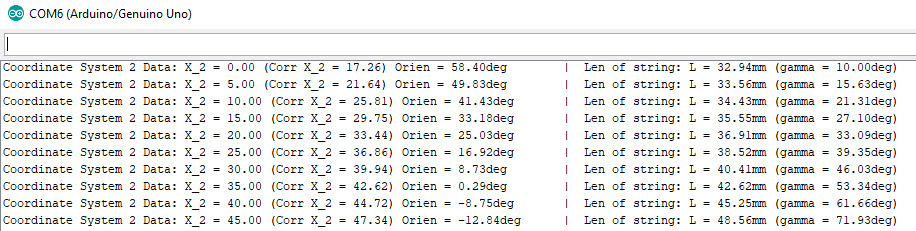
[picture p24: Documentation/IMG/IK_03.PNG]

\end{center}

The layout of the data follows suite. Instead of the angle of the motor, we derive the amount the driving string is shortened. Once again the data correlates to real world measurements. By calculating the length of the string, we are free to write any method to accompany our driving motor mechanism. In the case of the servo, we will simply wind a string around a disk. This data also considers the orientation of the previous system involving the proximal phalange. The input value is corrected and used for processing. 

The thumb is the simplest mechanism, we only have two equations, two inputs and two outputs. The formula provided above was coded into a method and reliably controls our motors.

\subsubsection{Communications}
The Arduino Nano communicates with the PC through the mini-B USB connection serial port. The connection is established in the setup() function by a method Serial.begin (). This method possess one argument, speed of serial connection (default is 9600 bits per second). The method Serial.print() prints data to the serial port as human-readable ASCII text.

Besides a direct PC connection through USB which is usually used for debugging, we may also connect wirelessly through a Bluetooth connection. For this we need an additional module for the Arduino. Arduino allows us to have multiple serial connections with different speeds, so the communication with a bluetooth device HC-6 is done through universal asynchronous receiver-transmitter (UART) on 2 pins: rx and tx (receiver and transmitter). This may be seen below.

\begin{figure}[!hb]
    \begin{minipage}[b]{0.49\textwidth}
    	\centering
		
		\captionof{figure}{Bluetooth Module Wiring}	   	
	\end{minipage}
    \hfill
    \begin{minipage}[b]{0.49\textwidth}
    	\centering
		
		\captionof{figure}{Bluetooth Module Code}   	
	\end{minipage}
\end{figure}

\break
\section{Hand Prototype}
With the kinematics and control method vigorously defined, we may put together a prototype for the mechanical hand and create simulations to test whether it will meet our requirements.

The mechanical hand needs to have the full dexterity of the human hand, which means that the mechanism dimensions need to be chosen so the range of motion is proper. Additionally, we must maintain the same speeds and accelerations as its flesh counterpart. For this it is important to select a lightweight material and motors. We may make use of an FDM printer to develop a versatile model out of PLA plastic. This solution is the fastest, cheapest and allows for rapid prototyping. The joints are made of smooth metal rods, which may help in fluid motion by reducing joint friction.

In order to assure our model is lightweight and has similar characteristics to the human hand, we needed to use compact, light but powerful motors. As motors can be rather expensive, we also needed to factor in price. We decided to go for SG92R as it fulfills enough requirements for the prototype and it is the best in its price range. Having 2.5kg*cm torque and 180deg movement range it is sufficient for demonstration of mechanics. Simulations in Solidworks confirm the geometry allows for velocities about half that of the real human hand. Below are two plots, one graphed by our hand, the other measurements taken from a human hand. We may see the velocity curve is similar, therefore our mechanics will allow for realistic movement. The peek speed was 414 mm/sec at about 45 degree angle in our situation.

\begin{figure}[!hb]
    \begin{minipage}[b]{0.49\textwidth}
    	\centering
		
		\captionof{figure}{Velocity Plot of Simulated Kinematics}	   	
	\end{minipage}
    \hfill
    \begin{minipage}[b]{0.49\textwidth}
    	\centering
		
		\captionof{figure}{Velocity Plot of Human Hand}   	
	\end{minipage}
\end{figure}

The inbuilt simulation software allows us to animate the assembly and check its range of motion. We also were able to obtain accelerations and displacements of each joint required to check if the kinematic model was correct. 

\begin{figure}[!hb]
    \begin{minipage}[b]{0.49\textwidth}
    	\centering
		
		\captionof{figure}{Acceleration Plot of Simulated Kinematics}	   	
	\end{minipage}
    \hfill
    \begin{minipage}[b]{0.49\textwidth}
    	\centering
		
		\captionof{figure}{Displacement Plot of Human Hand}   	
	\end{minipage}
\end{figure}

\break
With the requirements defined and various solutions provided, we may develop a model in CAD software. During the design process, we must keep in mind that the parts must be printable on a FDM printer. Our software of choice is Solidworks as it carries additional features such as simulations and renderings that may greatly assist us in the prototyping phase. Below we may view some images of the first prototype.

\begin{figure}[!hb]
    \begin{minipage}[b]{0.49\textwidth}
    	\centering
		
	\end{minipage}
    \hfill
    \begin{minipage}[b]{0.49\textwidth}
    	\centering
		
	\end{minipage}
\end{figure}

FEM analysis performed allowed us to find the maximum force a single finger can output. It is about 8.23N so when the filament Fiberflex 40D that will be covering the fingertips to increase the grip strength  we can grab objects in range of 100-400grams, depending on the material that it is from. See table below for multiplicands that set the output force. 

\begin{center}


\end{center}

Additional design considerations include a self locking mechanism, so when the hand is turned off, it keeps the open palm position. This is ensured by springs attached to the back of each finger and by servo holding torque.

\break
\section{Bills of Materials}
The below bills of materials includes all the materials used to build our working prototype. The prices provided are accessible market prices, and many of the elements where already owned or found at a lower price. The Kinect was kindly donated by Andrew Popiel from Lazy Solutions.

\begin{center}

\end{center}

\section{Future Development}
Based on the entire design process above, we may start putting together the concept for the final product. With properly working mechanics, we may continue by increasing the number of fingers. With the prototyping phase almost complete, we may also begin constructing a version with other materials. A concept was created in blender software to display the possibilities of such a hand.

\begin{figure}[!hb]
    \begin{minipage}[b]{0.49\textwidth}
    	\centering
		
	\end{minipage}
    \hfill
    \begin{minipage}[b]{0.49\textwidth}
    	\centering
		
	\end{minipage}
\end{figure}

\break
\addcontentsline{toc}{section}{References}
\begin{thebibliography}{1}
	\bibitem{bebionic} BeBionic. Retrieved from {\url{http://bebionic.com/the_hand/technical_information/}} 
	\bibitem{vincent} VincentSystems. Retrieved from {\url{  https://vincentsystems.de/en/}} 
	\bibitem{JRRD} U.S. Department of Veterans Affairs, {\em Journal of Rehabilitation Research And Development}. Volume 50 Number 5, 2013
   Pages 599-618 Retrieved form {\url{https://www.rehab.research.va.gov/jour/2013/505/page599.html}}
	\bibitem{stringHand} SOLIDWORKS. Retrieved from {\url{ http://blogs.solidworks.com/tech/2016/08/solidworks-time-lapse-tutorial-mechanical-hand.html}}
	\bibitem{airMuscle} Peter Scarfe, Euan Lindsay {\em Air Muscle Actuated Low Cost Humanoid Hand}. Retrieved from {\url{ http://cdn.intechopen.com/pdfs/4176/InTech-Air_muscle_actuated_low_cost_humanoid_hand.pdf
}} 
	\bibitem{kinect} Kinect. Retrieved from {\url{https://www.jameco.com/jameco/workshop/howitworks/xboxkinect.html}}
	\bibitem{Digits} DIGITS. Retrieved from {\url{https://spectrum.ieee.org/video/consumer-electronics/audiovideo/digits-hands-free-3d}}	
	\bibitem{ALTERA} Altera, Video and Image Processing Design Using FPGAs. Retrieved from {\url{https://www.altera.com/en_US/pdfs/literature/wp/wp-video0306.pdf}}
	\bibitem{CpuFpga} Brandon Treece ,VisionSystems Design. Retrieved from {\url{https://www.vision-systems.com/articles/print/volume-22/issue-8/features/cpu-or-fpga-for-image-processing-which-is-best.html	}}
	\bibitem{FPGA} FPGA in Robotics. Retrieved from {\url{https://robotics.stackexchange.com/questions/1153/when-should-fpgas-be-used-in-robotics}}
	\bibitem{CpuFpga02} APUs vs FPGAs. Retrieved from {\url{http://www.electronicdesign.com/microprocessors/apus-vs-fpgas-battle-smart-camera-processing-supremacy}}
	\bibitem{Intel} Intel FPGA SDK for OpenCL. Retrieved from {\url{https://www.altera.com/en_US/pdfs/literature/hb/opencl-sdk/aocl_programming_guide.pdf}}
	\bibitem{OpenCL} OpenCL. Retrieved from {\url{https://opencv.org/platforms/opencl.html}}
	\bibitem{VisionProcessing} Video and Image Processing Suite Intel FPGA IP. Retrieved from {\url{https://www.altera.com/products/intellectual-property/ip/dsp/m-alt-vipsuite.html}}
	\bibitem{Grip} A comparison of the grip force distribution in natural hands and in prosthetic hands. Retrieved from {\url{https://pdfs.semanticscholar.org/f600/c0ad7d6ecb7510b1b8e8f1318ffa03bb48cd.pdf}}
	\bibitem{LK01} Lucas-Kanade Tutorial Example 1 Retrieved from {\url{https://www.mathworks.com/matlabcentral/fileexchange/48744-lucas-kanade-tutorial-example-1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}}, version 1.0 by Zhiyuan
	\bibitem{ARDSerial} Arduino Serial Connection Retrieved from {\url{https://www.arduino.cc/en/Reference/SoftwareSerial}}
	\bibitem{MECHSTAT} Human Hand Kinematics Analysis Retrieved from {\url{
https://waset.org/publications/10000325/measurement-and-analysis-of-human-hand-kinematics}}

\end{thebibliography}
  
\end{document}

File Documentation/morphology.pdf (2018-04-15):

Aspect/Function | Option 1 | Option 2 | Option 3 | Option 4 | Option 5

Mechanical
EndEffector Type | 1DOF Clamping Mechanism | Suction Mechanism | Hook | 5 Finger Mechanical Hand | Jamming Mechanism
(Dexterity 1-10, Simplicity 1-5, Durability 1-5) | (2, 5, 5) = 12 | (2, 4, 3) = 9 | (1, 5, 5) = 11 | (10, 1, 2) = 13 | (8, 3, 2) = 13
Driving Mechanism | Direct Motor Drive | Indirect Motor Drive (Lines) | Pneumatic Drive | Hydralic Drive | Air Muscle
(Precision 1-10, Speed 1-10, Torque/Force 1-10, System Size 1-5) | (10, 10, 6, 5) = 31 | (10, 10, 6, 4) = 30 | (5, 10, 8, 1) = 24 | (5, 8, 10, 1) = 24 | (5, 10, 7, 3) = 25

Software
Kinematic Processing | Average PC | Microprocessor | FPGA | Cloud Computing | Analog Electronic Circuits
(Processing Power 1-10, Response Time 1-10,Size 1-10, Cost 1-10) | (8, 8, 4, 4) = 24 | (4, 8, 10, 10) = 32 | (8, 10, 8, 10) = 32 | (10, 3 10, 8) = 31 | (2, 10, 5, 6) = 23

Sensing
Endeffector Position Control | Accelometer and Gyroscope | Vision Control | Flex Sensor | Tensometers | Inductive Sensor
(Usability 1-5, Accuracy 1-10, Responsivness 1-10, Cost 1-5) | (4, 8, 9, 4) = 26 | (5, 6, 8, 5) = 24 | (4, 3, 7, 1) = 15 | (4, 1, 9, 2) = 16 | (3, 6, 8, 4) = 21
Option 6 | Option 7 | Option 8 | Option 9

Mechanical
EndEffector Type Precision Probes Excavater Bucket Three Fingered Hand Friction Gripper
(Dexterity 1-10, Simplicity 1-5, Durability 1-5) (5, 4, 3) = 12 (1, 5, 5) = 11 | (9, 2, 3) = 14 | (2, 4, 4) = 10

Driving Mechanism Smart material heat responsive Smart material electric sensitive
(Precision 1-10, Speed 1-10, Torque/Force 1-10, System Size 1-5) (3, 2, 4, 5) = 14 | (3, 4, 4, 5) = 16

Software
Kinematic Processing
(Processing Power 1-10, Response Time 1-10,Size 1-10, Cost 1-10)

Sensing
Endeffector Position Control Joystick Keyboards Artificial Inteligence Electrodes
(Usability 1-5, Accuracy 1-10, Responsivness 1-10, Cost 1-5) | (1, 8, 10, 3) = 22 | (4, 1, 10, 5) = 20 | (5, 6, 8, 5) = 24 | (5, 10, 10, 5) = 30

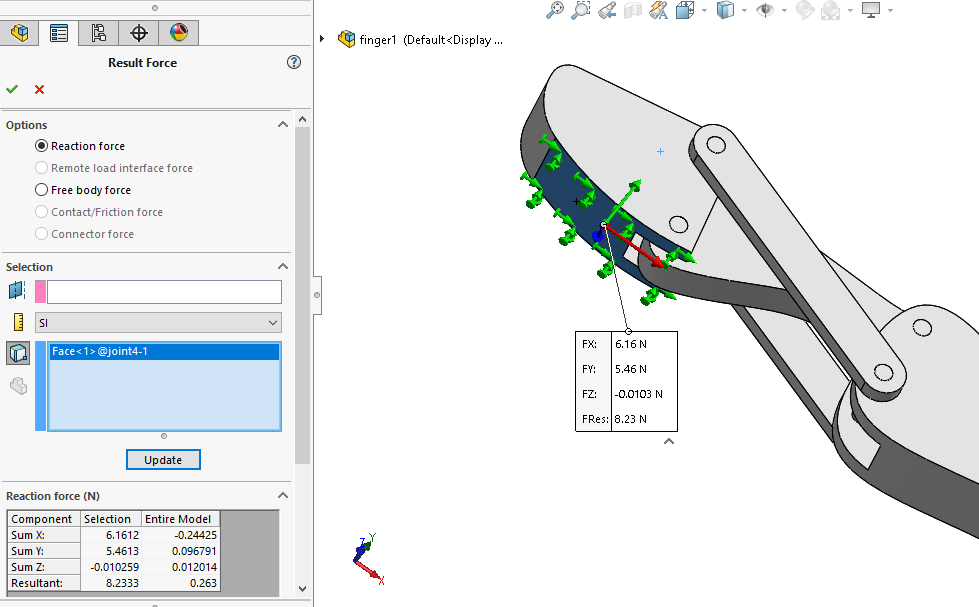
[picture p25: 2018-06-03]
Documentation/IMG/SOLID/reaction force.png

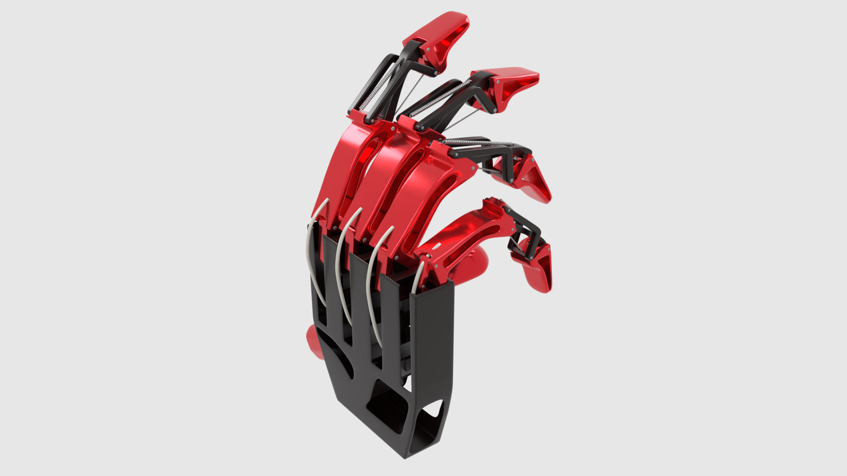
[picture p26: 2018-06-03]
Documentation/Render/MechHand6.png

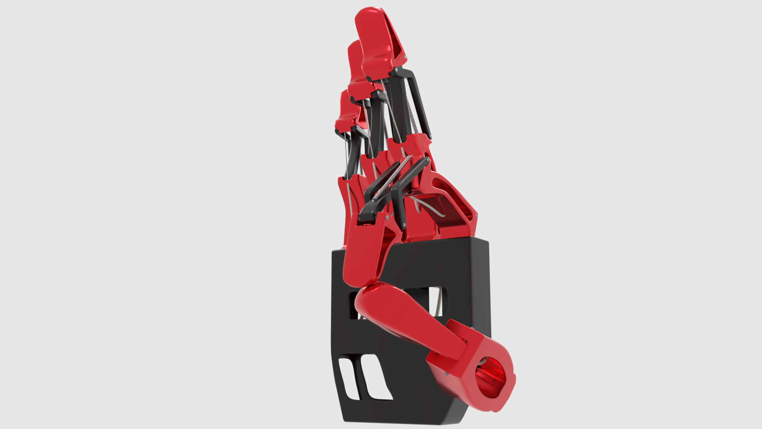
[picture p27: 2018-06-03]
Documentation/Render/MechHand8.png

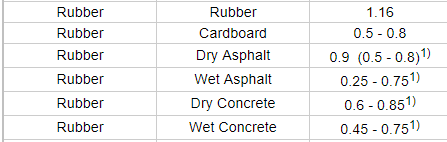
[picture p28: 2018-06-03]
Documentation/IMG/SOLID/frictioncoeffs.png

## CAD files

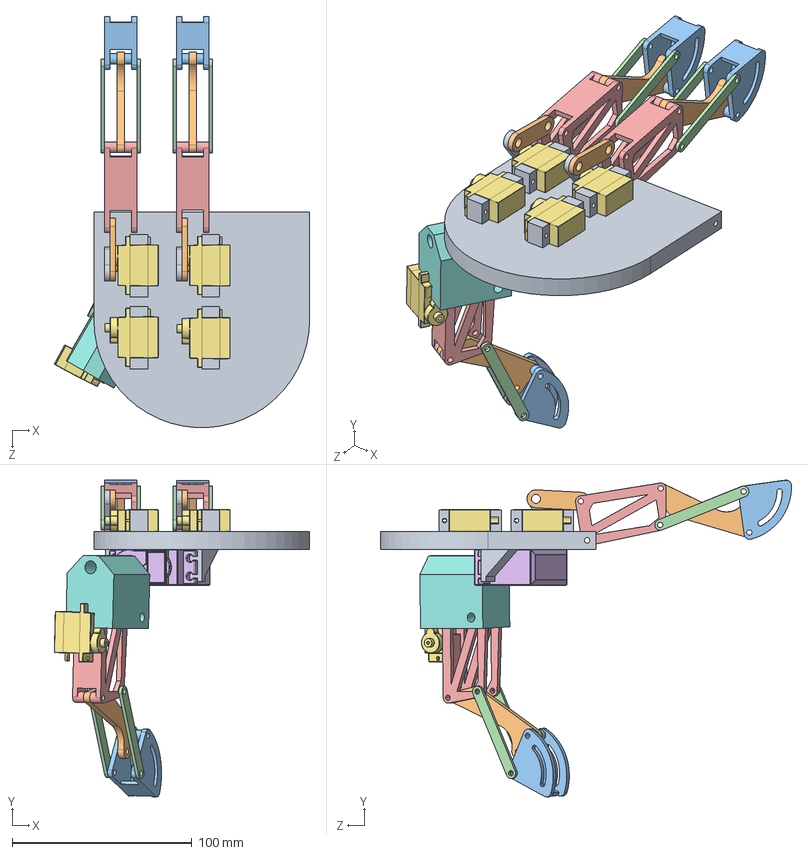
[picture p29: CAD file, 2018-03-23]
CAD_Model/hand.SLDASM
142.0 x 176.2 x 228.5 mm
base
[F1]ProximalPhalange x 3
[F1]DistalPhalange_Joint x 3
[F1]MedialPhalange_Lever x 6
[F1]MedialPhalange x 3
servo_motor.ipt
TowerPro SG92R Servo Motor x 5
joint
bar1 x 2
bar2 x 2

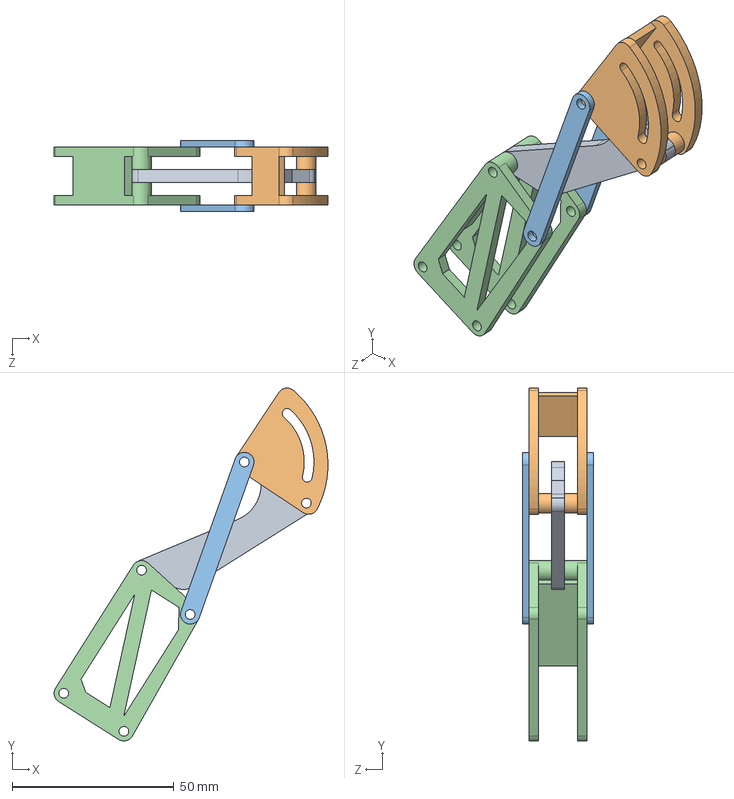
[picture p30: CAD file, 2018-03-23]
CAD_Model/assembly.SLDASM
84.6 x 109.1 x 22.0 mm
[F1]ProximalPhalange
[F1]DistalPhalange_Joint
[F1]MedialPhalange_Lever x 2
[F1]MedialPhalange

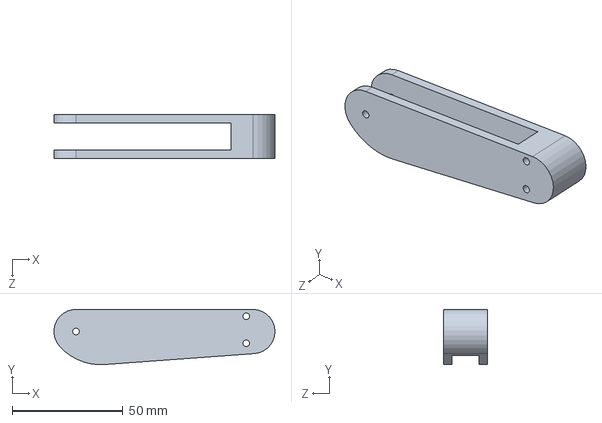
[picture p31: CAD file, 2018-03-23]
CAD_Model/thumb.SLDPRT
99.9 x 25.0 x 20.0 mm

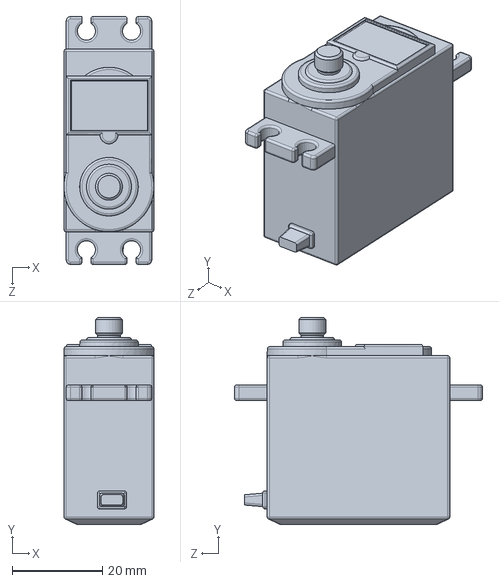
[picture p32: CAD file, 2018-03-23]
CAD_Model/servo_motor.ipt.SLDPRT
20.0 x 46.0 x 55.0 mm

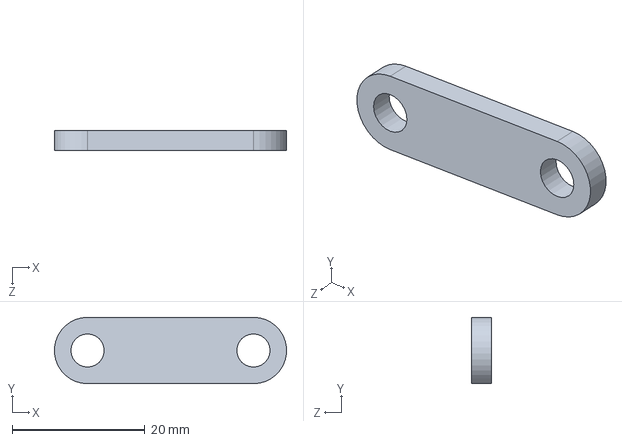
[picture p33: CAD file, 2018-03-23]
CAD_Model/bar2.SLDPRT
35.0 x 10.0 x 3.00 mm

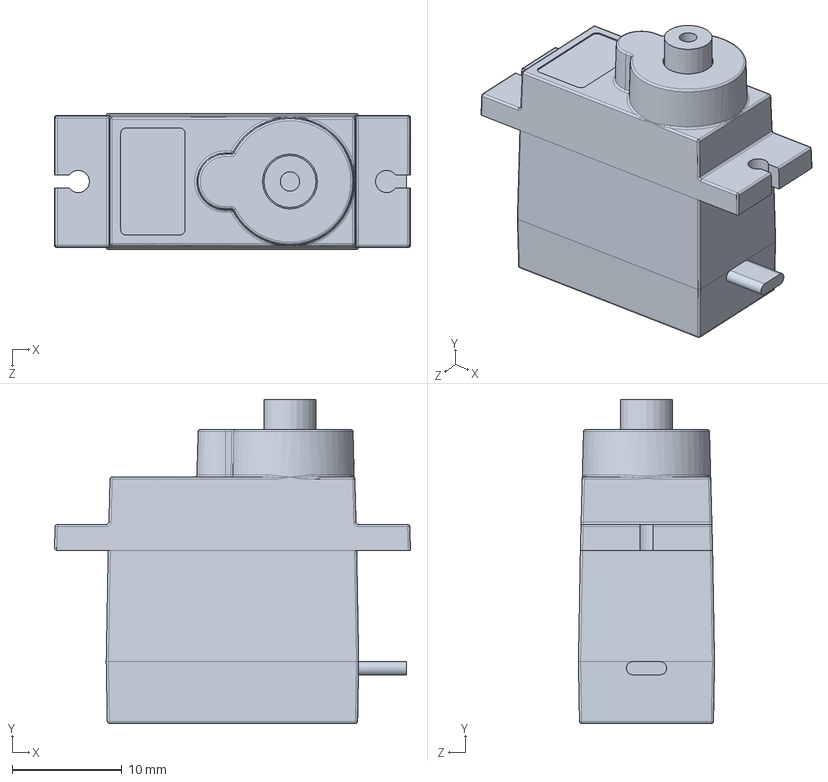
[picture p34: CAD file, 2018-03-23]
CAD_Model/TowerPro SG92R Servo Motor.SLDPRT
32.5 x 29.6 x 12.4 mm

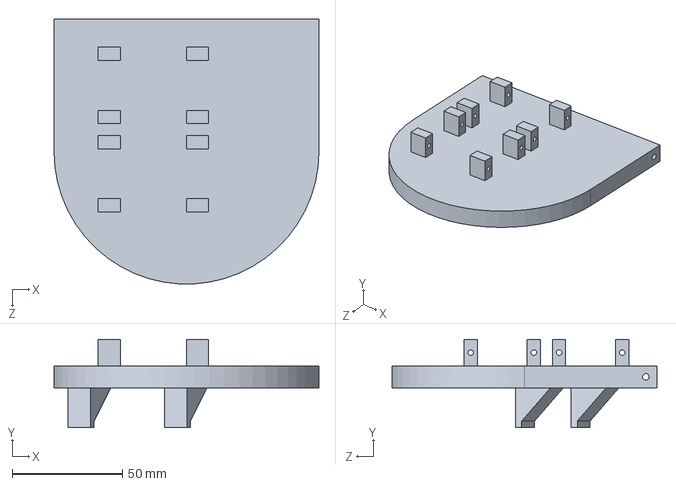
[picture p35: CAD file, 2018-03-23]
CAD_Model/base.SLDPRT
120.0 x 40.0 x 119.9 mm

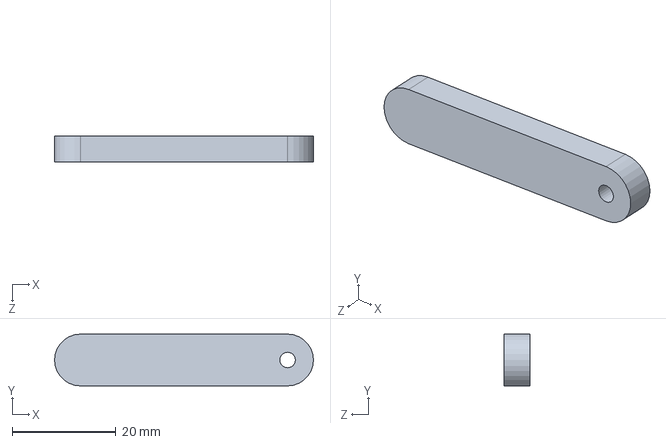
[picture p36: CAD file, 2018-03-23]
CAD_Model/thumb_tip.SLDPRT
50.0 x 10.0 x 5.00 mm

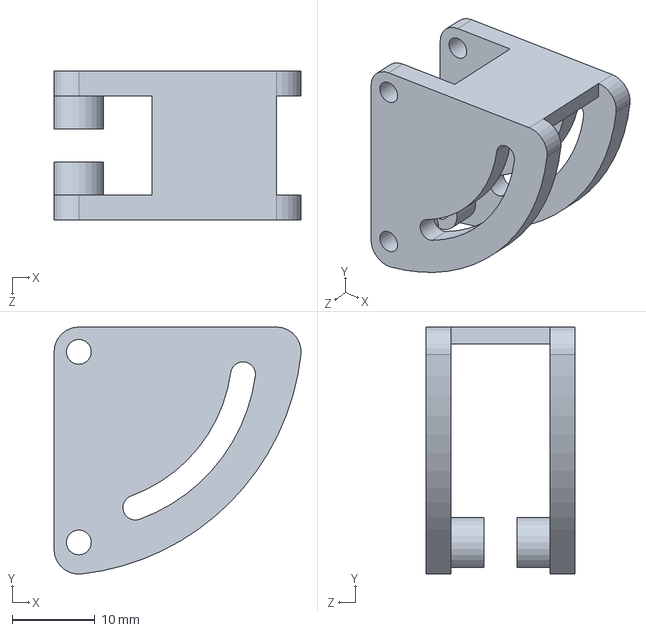
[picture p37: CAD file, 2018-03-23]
CAD_Model/[F1]DistalPhalange_Joint.SLDPRT
29.8 x 29.8 x 18.0 mm

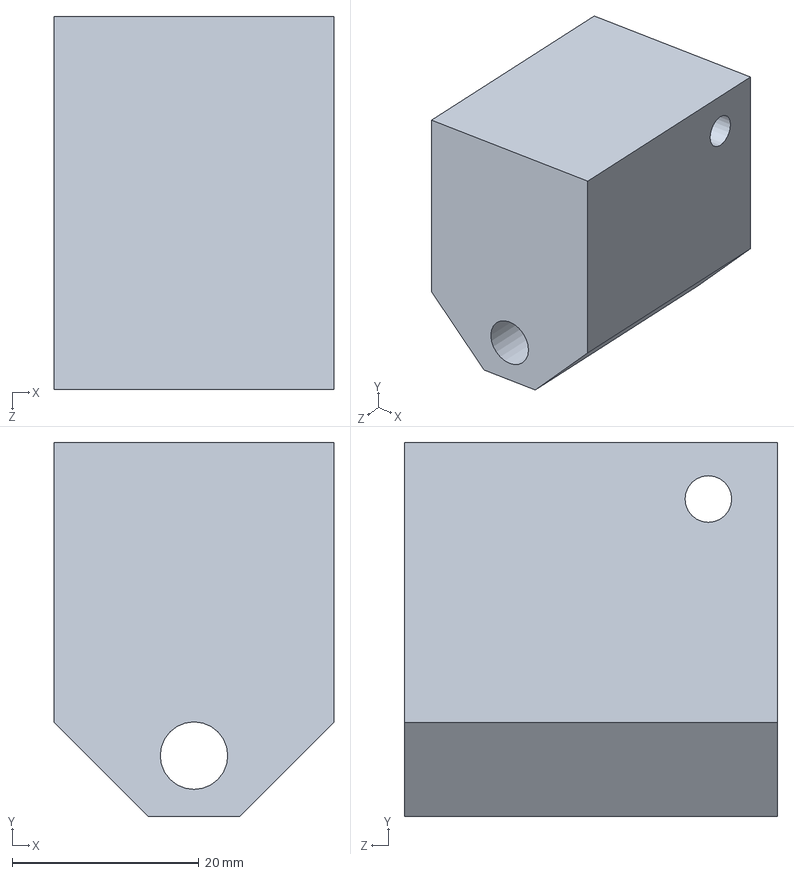
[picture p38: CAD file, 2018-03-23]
CAD_Model/joint.SLDPRT
30.0 x 40.1 x 40.0 mm

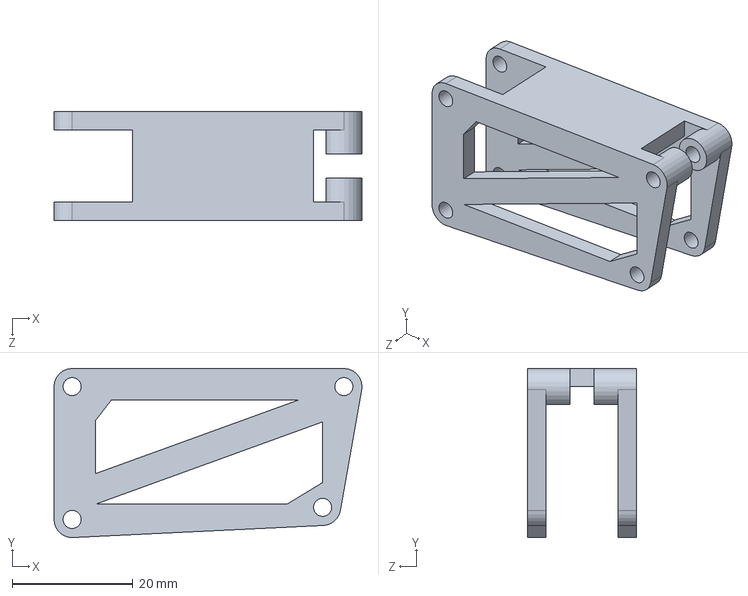
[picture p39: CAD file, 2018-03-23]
CAD_Model/[F1]MedialPhalange.SLDPRT
51.0 x 28.0 x 18.0 mm

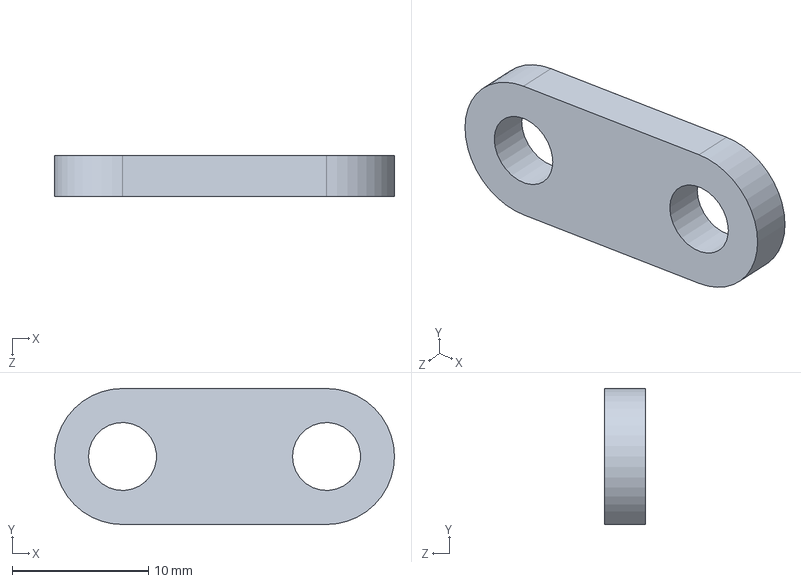
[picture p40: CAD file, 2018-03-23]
CAD_Model/bar1.SLDPRT
25.0 x 10.0 x 3.00 mm

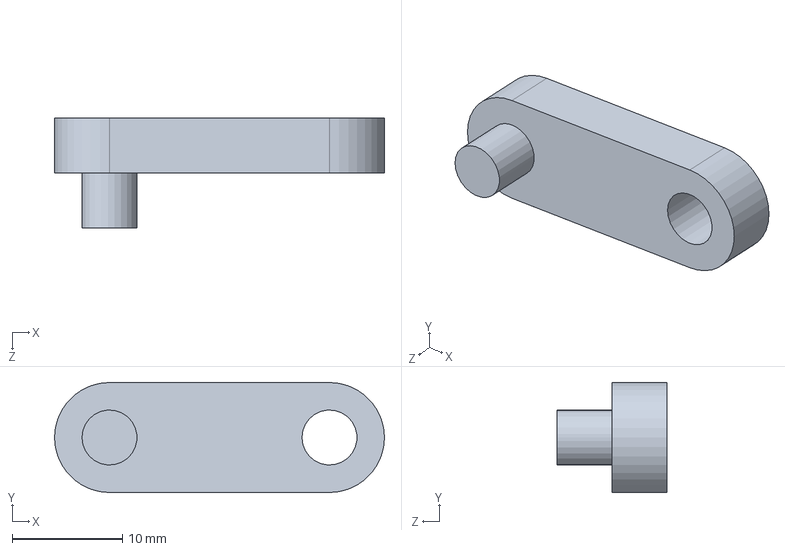
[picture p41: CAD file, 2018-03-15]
CAD_Model/joint20.SLDPRT
30.0 x 10.0 x 10.0 mm

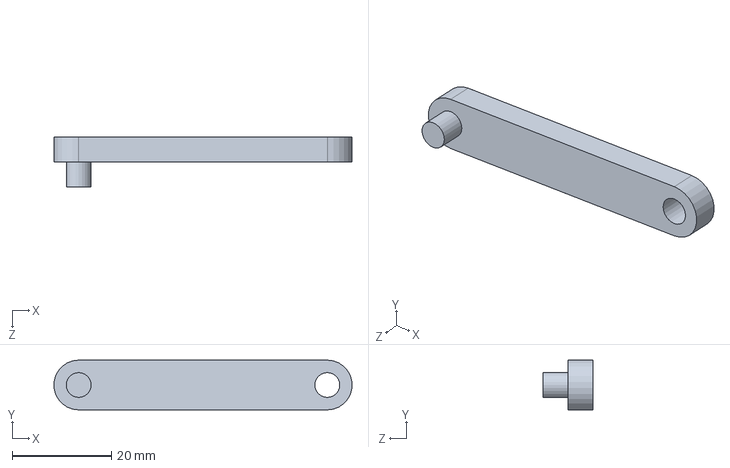
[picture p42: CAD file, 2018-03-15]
CAD_Model/joint40.SLDPRT
59.9 x 10.0 x 10.0 mm

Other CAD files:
CAD_Model/[F1]MedialPhalange_Lever.SLDPRT
CAD_Model/[F1]DistalPhalange.SLDPRT
CAD_Model/joint30.SLDPRT
CAD_Model/[F1]ProximalPhalange.SLDPRT
CAD_Model/CameraSlider/ASM.prt
CAD_Model/CameraSlider/BackCover - Copy.prt
CAD_Model/CameraSlider/BackCover.prt
CAD_Model/CameraSlider/FrontCover.prt
CAD_Model/DiopticCameraRig/FixedRig.prt
NX/F1_ASM.prt
NX/F1_DP_001.prt
NX/F1_DP_002.prt
NX/F1_MP_001.prt
NX/F1_MP_002.prt
NX/F1_PP_001.prt

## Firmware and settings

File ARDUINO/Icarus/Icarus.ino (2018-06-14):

#include <Servo.h>

//First Finger Motors
Servo motor01, motor02;
//Second Finger Motors
Servo motor03, motor04;
//Thumb Motors
Servo motor05, motor06;

int servo_position = 0;

const double rad2deg = 180/PI;
const double deg2rad = PI/180;

//Motor 1
double theta,phi;
double coord_1_X,coord_1_ang;
//Motor 2
double gamma,len;
double coord_2_X,coord_2_ang;
//Thumb Motors
double theta1,theta2;

//temp input values
double X_1 = 54; //Domain [0,A_2]
double X_2 = 30; //Domain [-a,X_1+b]
double X_3 = 1;
double X_4 = 1;
double ang_H = 0 *deg2rad; //Domain [-90,90] Rad

unsigned i = 0;

bool flag = 0;

void setup() {
  Serial.begin(57600);
  motor01.attach(2);  
  motor02.attach(4);
  motor03.attach(6);  
  motor04.attach(8);
  motor05.attach(10);  
  motor06.attach(12);
}

void loop() {
/* First Motor Calculations (INVERSE)
 * X_1 - First coordinate point
 * phi - Angle of first motor
 */
  theta = calc_sys_2(X_1,ang_H,i);
  phi = calc_sys_1(theta,i);
/* Save data for first coordinate data (FORWARD)
 * This gives us the new coordinate system
 * for the next set of systems.
 */
  coord_1_ang = calc_orien_coord_1(theta,i);
  coord_1_X = calc_pos_coord_1(coord_1_ang,i);

  display_IK_Index_A(X_1,theta,phi,coord_1_ang,coord_1_X);

  //Second Motor
  //calc_sys_4(X_2,i);
  gamma = calc_sys_3_ang(X_2,coord_1_ang,ang_H,i); //X_2,coord_1_X,ang_H
  len = calc_sys_3_len(gamma,i);

  coord_2_ang = calc_orien_coord_2(gamma,len,i);
  coord_2_X = calc_pos_coord_2(coord_2_ang,len);

  display_IK_Index_B(X_2,gamma,len,coord_2_ang, coord_2_X);

  theta2 = calc_thumb_B(X_4,0);
  theta1 = calc_thumb_A(X_3,theta2,0);

  display_IK_Thumb(X_3,X_4,theta1,theta2);
  delay(500);

/*
  //motor01.write(-180);
  //delay(10);

*/
//Motor Control
  motor01.write(173-phi*rad2deg);
  motor03.write(190-phi*rad2deg);
  delay(15);


  if(X_1==54) flag = 1;
  if(X_1==0) flag = 0;
  if(flag==0)
    X_1 = X_1 + 1;
  else
    X_1 = X_1 - 1;
    
  if(X_2<45)
    X_2 = X_2 + 1;
  else
    X_2 = 0;
}

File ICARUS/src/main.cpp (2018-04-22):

#include <termios.h>
#include "../include/DisparityEye.h"
#include "../include/GUI.h"
#include "../include/Tracking.h"

using namespace std;

void disparity();
void tracking();
void restore_terminal_settings(void);
void disable_waiting_for_enter(void);
static struct termios oldt; //getchar without pressing enter

int main( int argc, const char** argv)
{
  GUI gui;

  unsigned choice;
  disable_waiting_for_enter();

  string option[3];
  option[0] = "Disparity Mapping";
  option[1] = "Tracking";
  option[2] = "Exit";

  bool loop = true;
  while(loop == true){
    choice = gui.Menu("", option, sizeof option/sizeof option[0]);
        printf("a");

    switch(choice){
      case 0: disparity(); break;
      case 1: tracking(); break;
      case 2: loop = false; break;
      default: loop = false;
    }
  }

  printf("\033[2J\033[1;H\033[?25l");
  
  return 0;
}


void disparity(){
  DisparityEye sight;
  sight.GUI();
}

void tracking(){
  Tracking track;
  track.GUI();
}

void restore_terminal_settings(void){
    tcsetattr(0, TCSANOW, &oldt);  /* Apply saved settings */
}

void disable_waiting_for_enter(void){
    struct termios newt;

    /* Make terminal read 1 char at a time */
    tcgetattr(0, &oldt);  /* Save terminal settings */
    newt = oldt;  /* Init new settings */
    newt.c_lflag &= ~(ICANON | ECHO);  /* Change settings */
    tcsetattr(0, TCSANOW, &newt);  /* Apply settings */
    atexit(restore_terminal_settings); /* Make sure settings will be restored when program ends  */
}

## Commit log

2018-03-10 Camera Calibration
2018-03-11 CAD Concept
    [assembly.SLDASM, bar.SLDPRT, dik.SLDPRT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]
2018-03-12 Fixed Names
    [[F1]DistalPhalange.SLDPRT, [F1]DistalPhalange_Joint.SLDPRT, [F1]MedialPhalange.SLDPRT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]
2018-03-16 Depth Map Calibration Features
2018-03-16 Extrinsic Parameter Calibration
2018-05-08 Inverse Kinematics
